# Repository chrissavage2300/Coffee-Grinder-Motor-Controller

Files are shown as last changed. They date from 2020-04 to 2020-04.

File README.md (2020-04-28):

# Coffee-Grinder-Motor-Controller

This is just a simple project where I retrofitted a hand crank grinder with a powerful gear motor.

Motor Used: https://www.servocity.com/118-rpm-hd-premium-planetary-gear-motor

Angle Bracket: https://www.servocity.com/90-single-angle-short-channel-bracket

Mount: https://www.servocity.com/hd-premium-planetary-gear-motor-mount-face-thru-hole

The software works as follows: Ramps up within a second or two from 25% to 100% full speed and then counts when the current goes below a minimum value. Once the current goes below that value, it shuts the motor off and waits for the user to press a button again. I had to measure the current using debugging and then average it out in excel to find a minimum value for when the coffee is ground.  During grinding the current is mostly higher than this min, so it wont trigger, but when the grinder is idling, it will hit that minumum more often. 

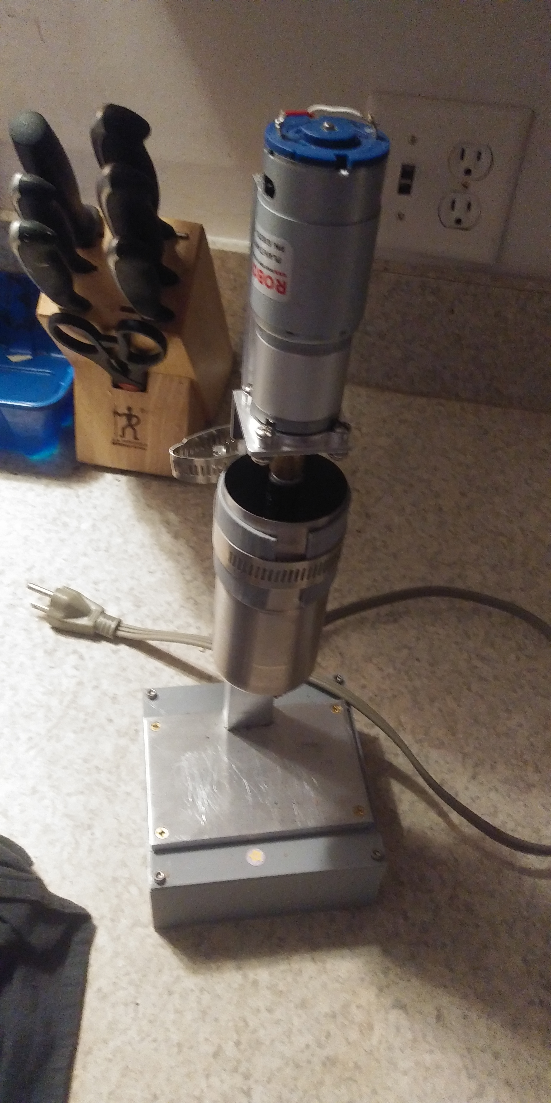
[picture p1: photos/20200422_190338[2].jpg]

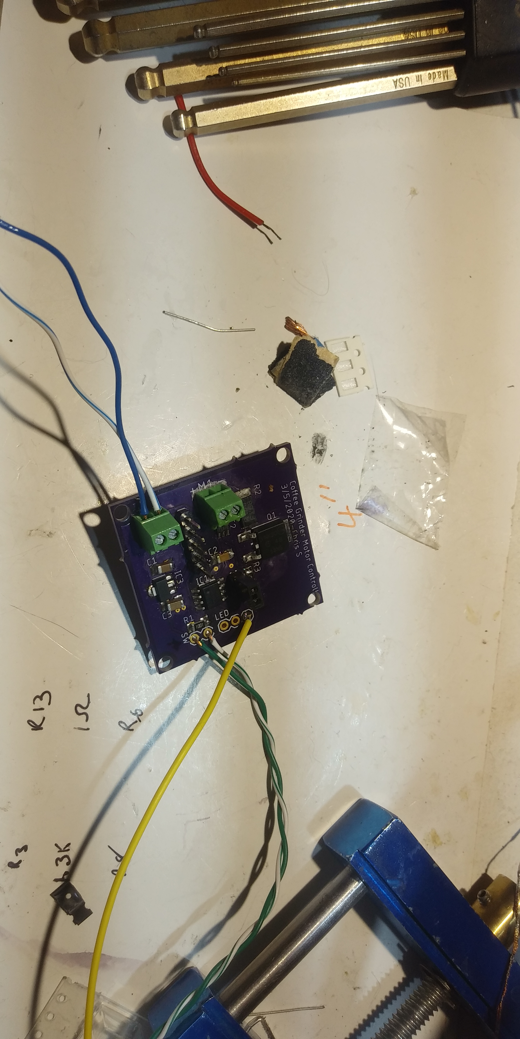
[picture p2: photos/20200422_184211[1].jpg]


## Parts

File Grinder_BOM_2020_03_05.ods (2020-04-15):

Part | Value | Device | Package | Description
C1 | 10uF | C-USC1206 | C1206 | CAPACITOR, American symbol
C2 | 0.1uF | C-USC1206 | C1206 | CAPACITOR, American symbol
C3 | 1uF | C-USC1206 | C1206 | CAPACITOR, American symbol
IC1 | PIC12F1840/SN | PIC12F1840/SN | SOIC8-SN | Low pincount microcontroller | Stock
IC2 | INA180A1 | INA180A1 | SOT23-5 | Current Sense IC
IC3 | 78L05F | 78L05F | SOT89 | POSITOIV-VOLTAGE REGULATORS
JP3 | 5 Pin Header | M05LOCK | 1X05_LOCK | 5 Pin Header, 0.1" | Stock
JP6 | Header | M02LOCK | 1X02_LOCK | Solder Direct
LED | Header | M03PTH | 1X03 | Solder Direct
M1 | Screw Header | M02POLAR | MOLEX-1X2 | Standard 2-pin 0.1 header. Use with" | Stock
Q1 | NTD4858 | MOSFET-NCHANNELFDD8780 | DPAK | Common NMOSFET Parts | Check Stock
R1 | 1K | R-US_R1206 | R1206 | RESISTOR, American symbol | Stock
R2 | 0.1 | R-US_R2512 | R2512 | RESISTOR, American symbol
R3 | 2k | R-US_R1206 | R1206 | RESISTOR, American symbol | Stock
SW | Header | M02LOCK | 1X02_LOCK | Solder Direct | Stock
VIN | Screw Header | M02POLAR | MOLEX-1X2 | Standard 2-pin 0.1 header. Use with" | Stock

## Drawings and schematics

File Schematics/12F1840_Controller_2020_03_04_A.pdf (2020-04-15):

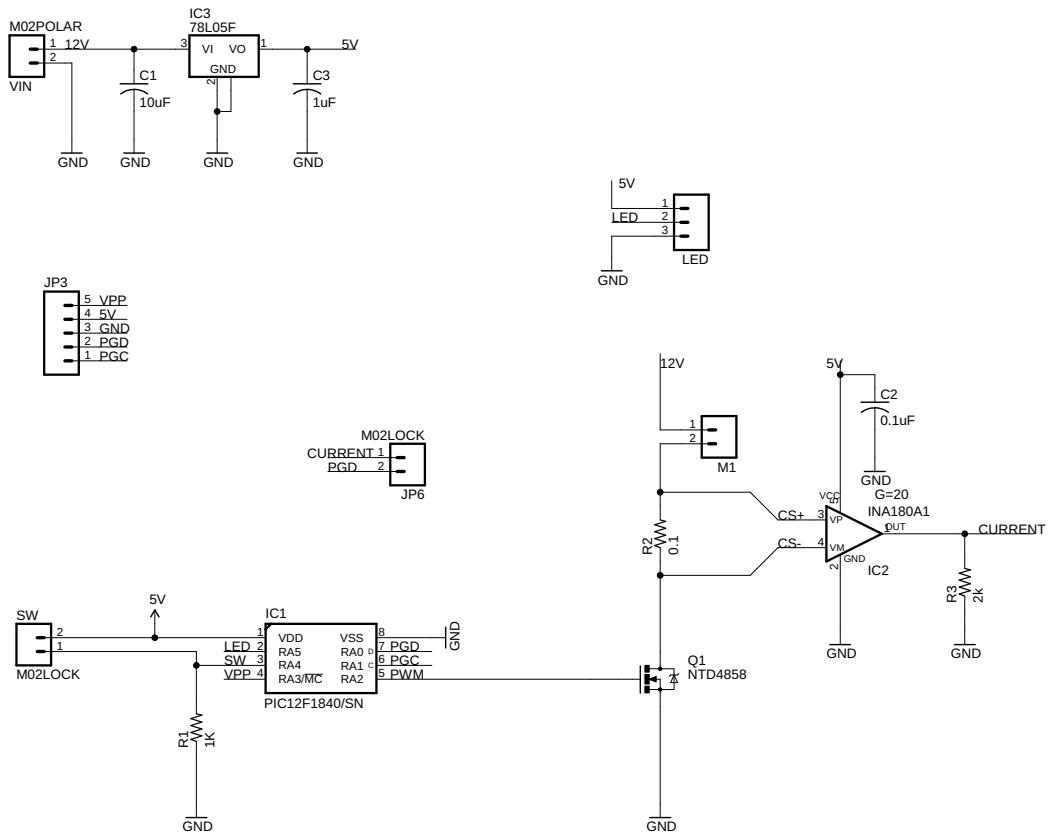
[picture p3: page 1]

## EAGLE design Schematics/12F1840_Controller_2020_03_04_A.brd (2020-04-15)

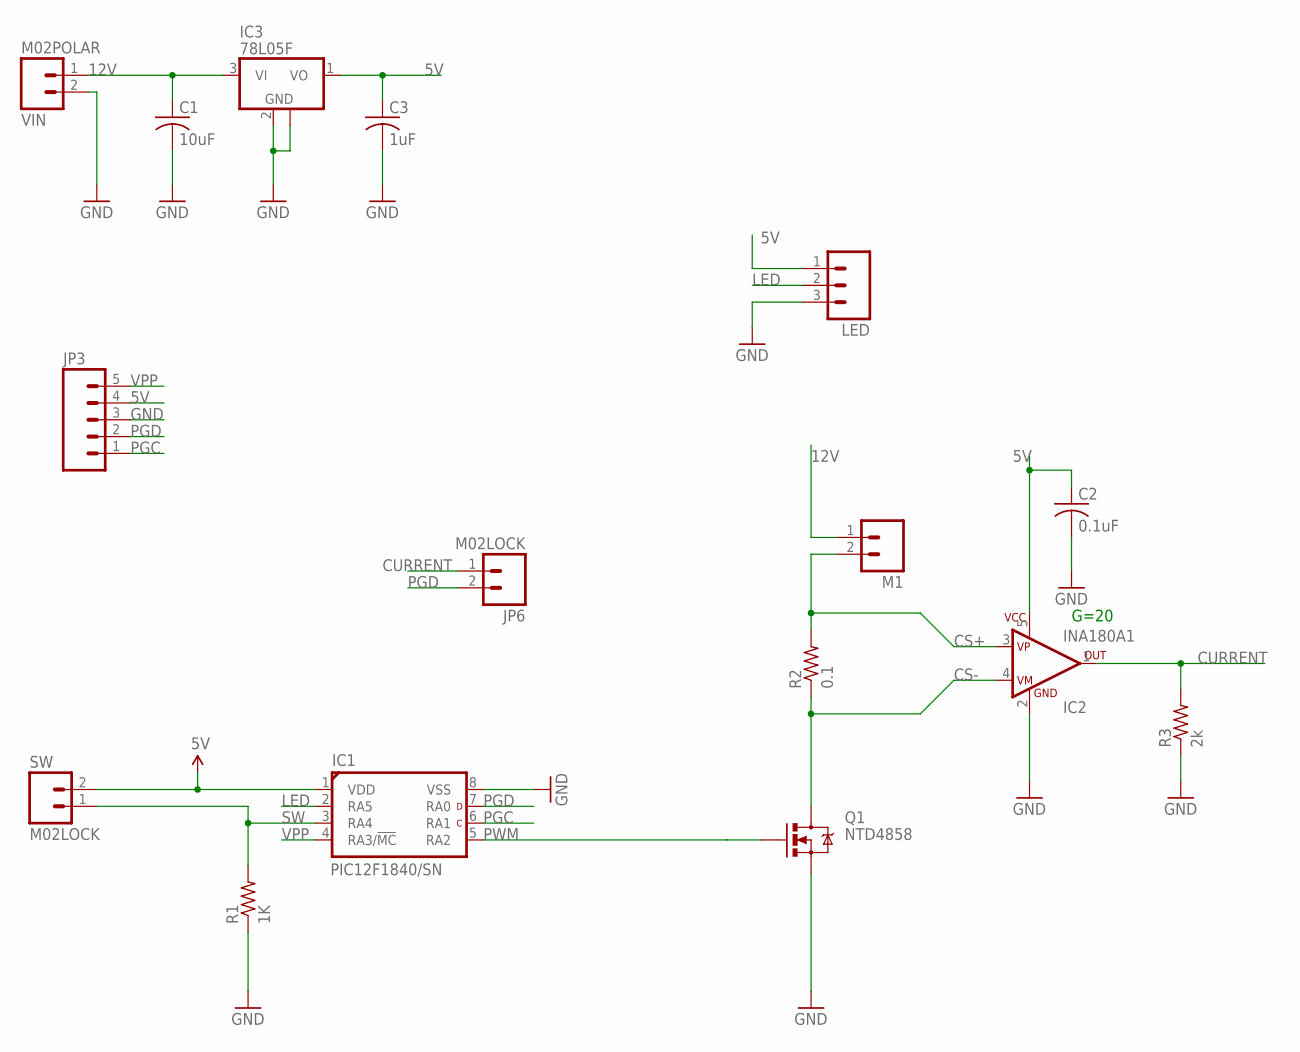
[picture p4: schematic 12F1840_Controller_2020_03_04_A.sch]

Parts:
C1: 10uF; C1206
C2: 0.1uF; C1206
C3: 1uF; C1206
IC1: PIC12F1840/SN; SOIC8-SN
IC2: INA180A1; SOT23-5
IC3: 78L05F; SOT89
JP3: M05LOCK; 1X05_LOCK
JP6: M02LOCK; 1X02_LOCK
LED: M03PTH; 1X03
M1: M02POLAR; MOLEX-1X2
Q1: NTD4858; DPAK
R1: 1K; R1206
R2: 0.1; R2512
R3: 2k; R1206
SW: M02LOCK; 1X02_LOCK
VIN: M02POLAR; MOLEX-1X2

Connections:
5V: C2.1, C3.1, IC1.1 (VDD), IC2.5 (V+), IC3.1 (VO), JP3.4, LED.1, SW.2
12V: C1.1, IC3.3 (VI), M1.1, VIN.1
CS+: IC2.3 (VP), M1.2, R2.2
CS-: IC2.4 (VM), Q1.4 (D), R2.1
CURRENT: IC2.1 (OUT), JP6.1, R3.2
GND: C1.2, C2.2, C3.2, IC1.8 (VSS), IC2.2 (V-), IC3.2 (GND), IC3.2@1 (GND), JP3.3, LED.3, Q1.3 (S), R1.1, R3.1, VIN.2
LED: IC1.2 (RA5), LED.2
PGC: IC1.6 (RA1), JP3.1
PGD: IC1.7 (RA0), JP3.2, JP6.2
PWM: IC1.5 (RA2), Q1.1 (G)
SW: IC1.3 (RA4), R1.2, SW.1
VPP: IC1.4 (RA3/!MC!), JP3.5

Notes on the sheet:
G=20

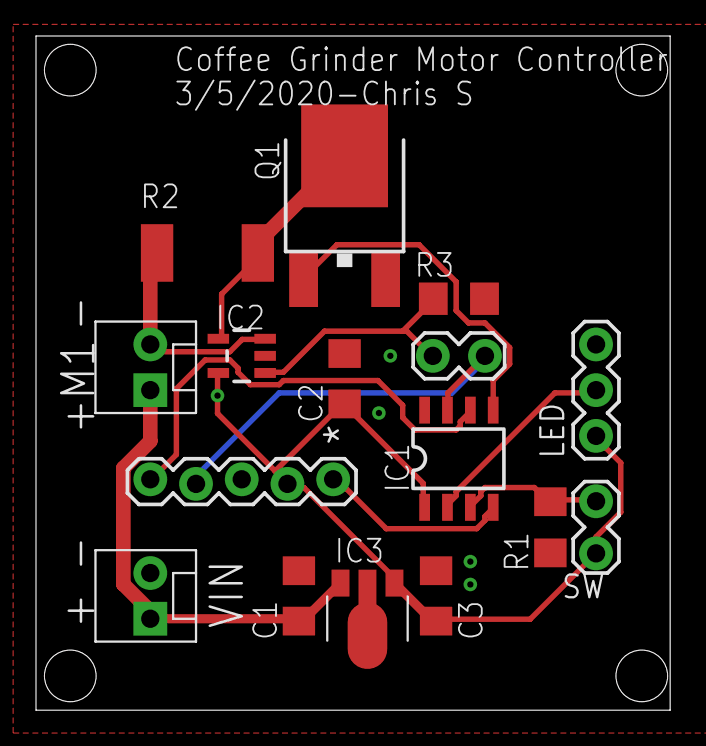
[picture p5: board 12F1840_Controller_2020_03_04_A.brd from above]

Board: 2 copper layers, 35.2 x 37.5 mm, 16 parts (0 on the bottom side), 12 nets.

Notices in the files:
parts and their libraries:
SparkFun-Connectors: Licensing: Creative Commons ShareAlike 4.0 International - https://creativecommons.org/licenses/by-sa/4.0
